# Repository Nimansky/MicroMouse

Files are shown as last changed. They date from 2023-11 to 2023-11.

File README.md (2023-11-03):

# MicroMouse - Readme

A [MicroMouse](https://en.wikipedia.org/wiki/Micromouse) built for a university school project by Nima Baradaran Hassanzadeh, Xian Chen and Christian Förster. The mouse is based on a Raspberry Pi 3B paired with an extension board hosting a STM32F030CC. As such, this project heavily involves sensor communication via I2C, inter-processor communication via UART, as well as a lot of STM32-internal timer and PWM logic. For exact specifics, please feel free to read the [documentation](/documentation.pdf)!

# Pinouts

| MCU Pin | Mode | GPIO Pin | Description |
|---|---|---|---|
| PF0 | Input | GPIO6 | Sensor links vorn |
| PC14 | Input | GPIO7 | Sensor rechts vorn |
| PC13 | Input | GPIO4 | Sensor links Seite |
| PB7 | Input | GPIO5 | Sensor rechts Seite |
| PB14 | TIM15 CH1 | GPIO0 | PWM Motor rechts (IN1) |
| PB15 | TIM15 CH2 | GPIO1 | PWM Motor rechts (IN2) |
| PB0 | TIM3 CH3 | LED1 | PWM Motor links (IN1)  |
| PB1 | TIM3 CH4 | LED2 | PWM Motor links (IN2)  |
| PA1 | EXTI Interrupt | GPIO13 | Motor Encoder rechts A |
| PC15 | EXTI Interrupt | GPIO14 | Motor Encoder links A  |
| PA0 | EXTI Interrupt | GPIO11 | Motor Encoder rechts B |
| PA2 | EXTI Interrupt | GPIO12 | Motor Encoder links B  |
| PB8 | I2C | SCL | Analog Sensor i2c SCL  |
| PB9 | I2C | SDA | Analog Sensor i2c SDA  |

# Communcation protocol

In order for the STM32 to be able to abstract away movement and the sensors from the actual solving algorithm, we had to come up with our own communication protocol.

## from master to mouse
    0x1A4 : Initiation sequence
    half byte : command type (current commands range from 0000-0100)
    32 bit param (padding if none needed)

## from mouse to master
    0x1A4 : Initiation sequence
    half byte : sensor (current sensors range from 0000-0110)
    32 bit sensor data

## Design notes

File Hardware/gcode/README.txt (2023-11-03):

Those parts were printed with a slightly modified Creality Ender 5 running Klipper.

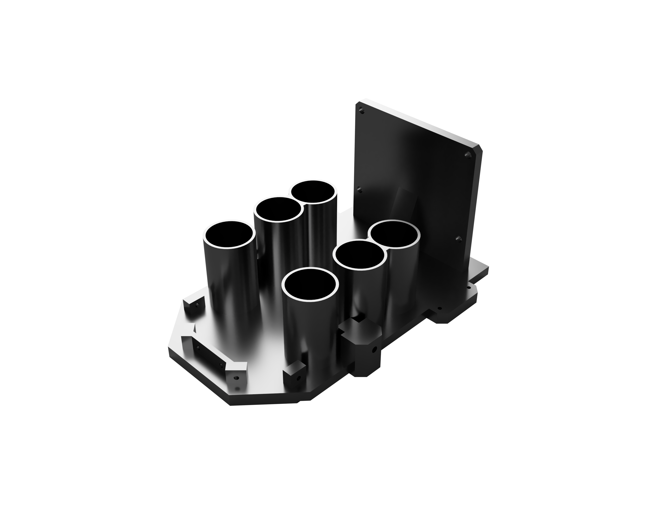
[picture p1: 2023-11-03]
Hardware/pictures/uMouse_base_plate.png

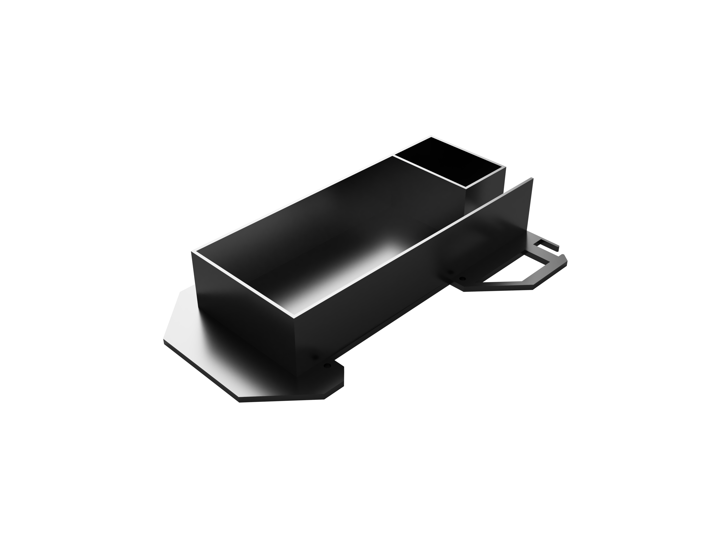
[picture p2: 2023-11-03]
Hardware/pictures/uMouse_top_plate.png

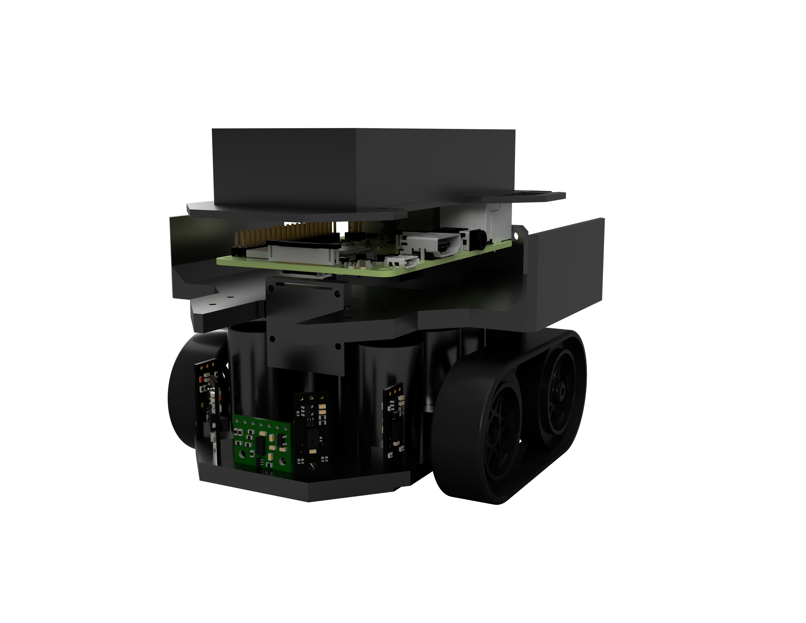
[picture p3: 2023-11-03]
Hardware/pictures/uMouse_total.png

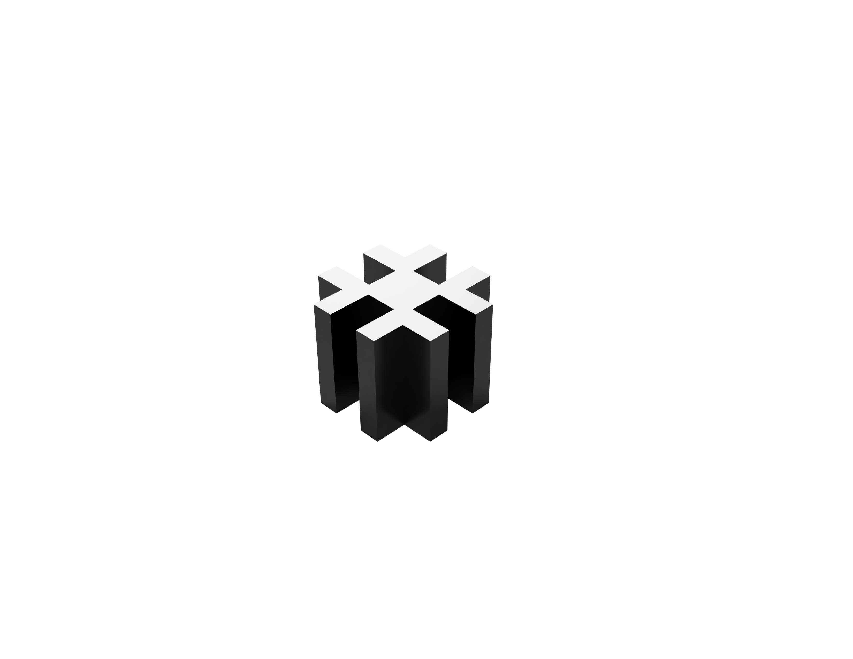
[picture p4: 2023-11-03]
Hardware/pictures/maze_connector.png

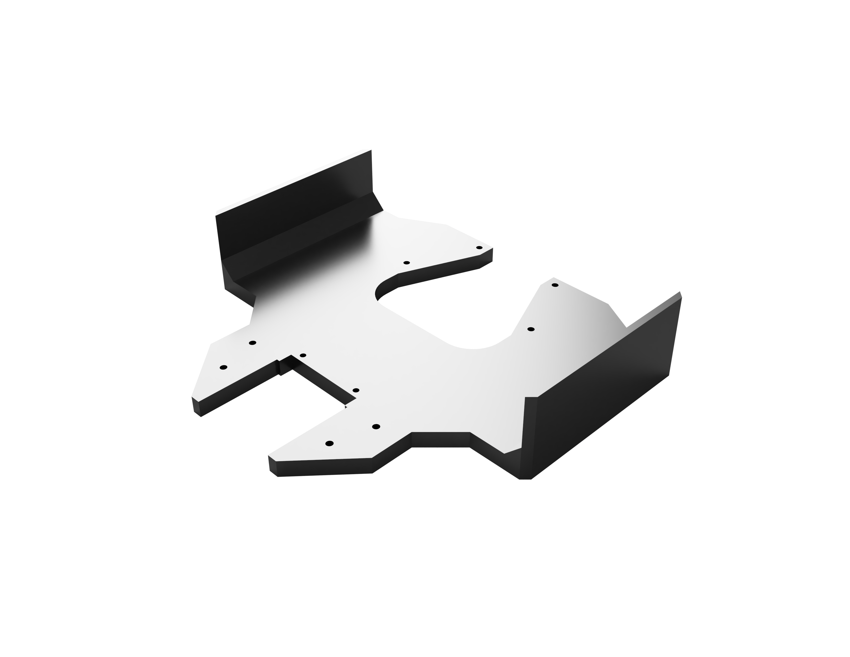
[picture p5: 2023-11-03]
Hardware/pictures/uMouse_mid_plate.png

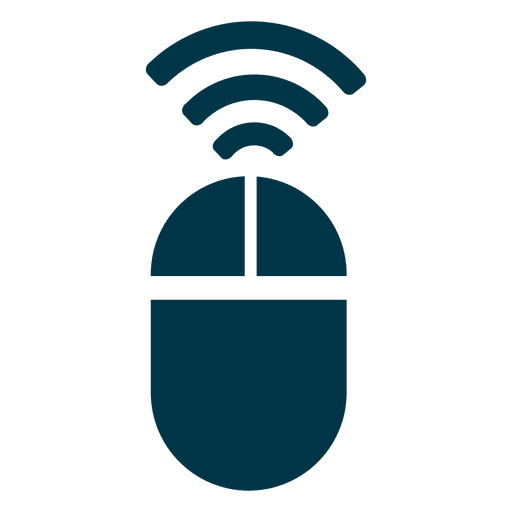
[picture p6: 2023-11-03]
Maze_Algorithm/res/mouse.png

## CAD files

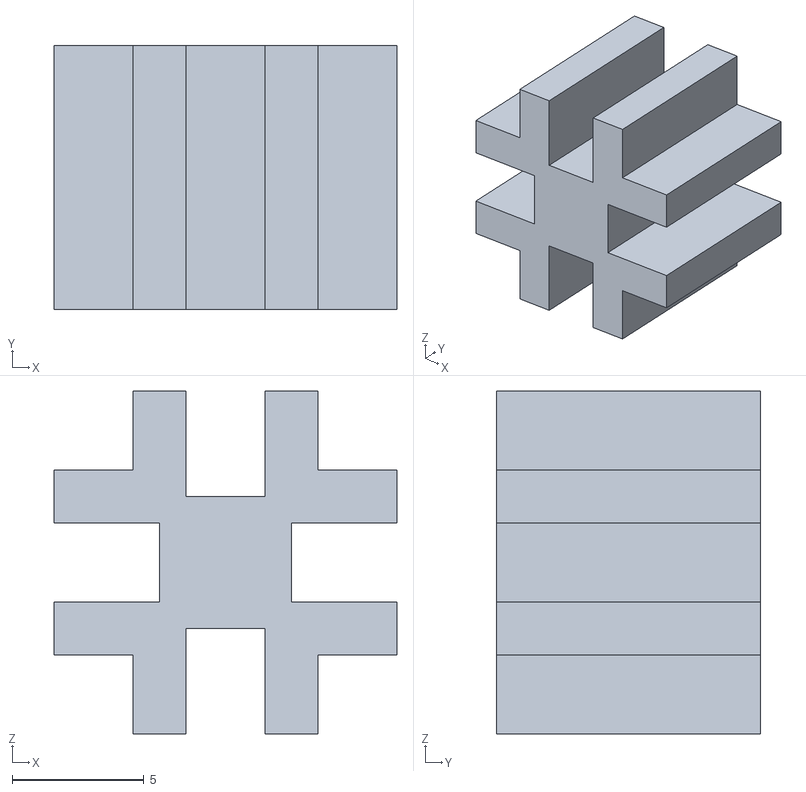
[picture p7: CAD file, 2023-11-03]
Hardware/models/maze_connector/maze_connector_v1.stl
13.0 x 10.0 x 13.0

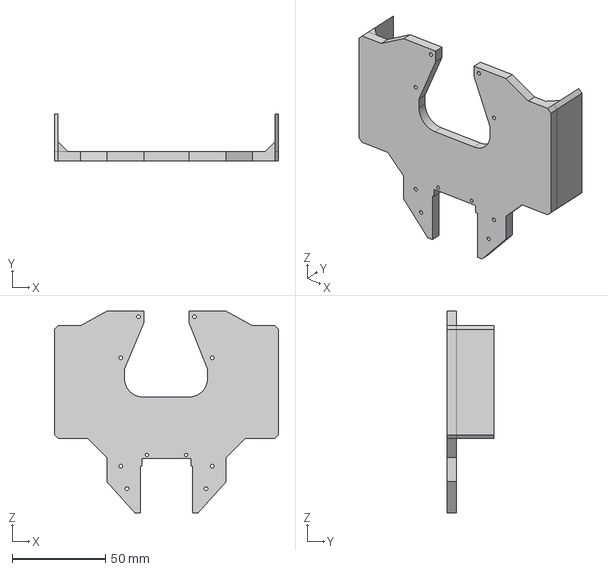
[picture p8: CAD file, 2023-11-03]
Hardware/models/mid_plate/mid_plate_v2.step
120.0 x 25.0 x 108.0 mm

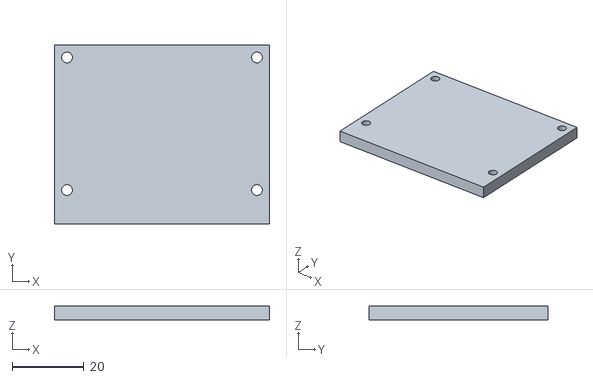
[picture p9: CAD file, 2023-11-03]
Hardware/models/misc/psu_mounting_test.stl
60.0 x 50.0 x 4.00

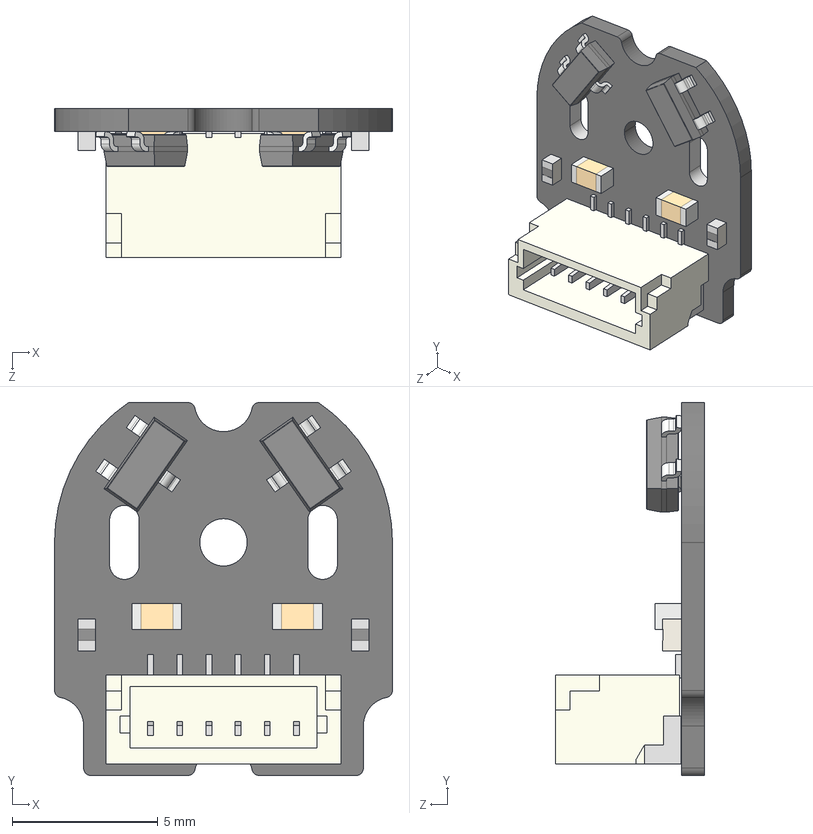
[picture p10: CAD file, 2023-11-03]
Hardware/models/pololu-4760-4761-models/magnetic-encoder-with-top-entry-connector-for-micro-metal-gearmotors.step
11.6 x 12.8 x 5.11 mm

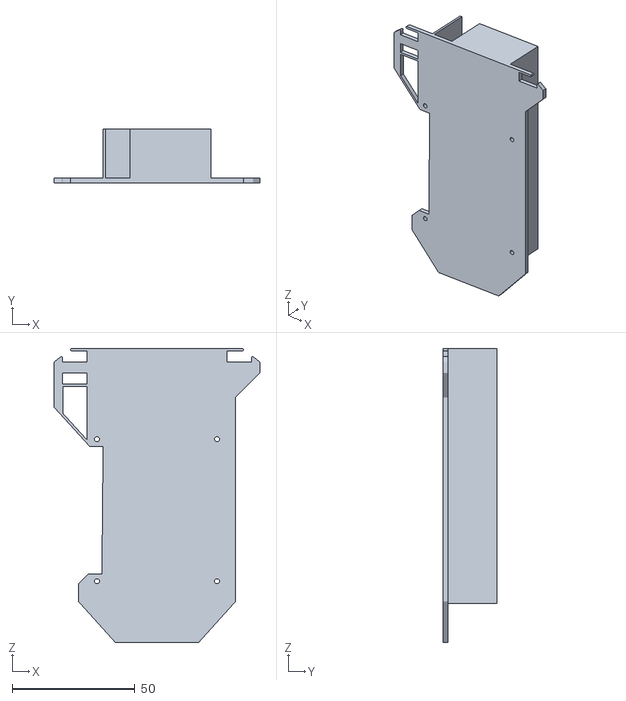
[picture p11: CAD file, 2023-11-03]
Hardware/models/top_plate/beta_top_plate_v2.stl
84.0 x 22.0 x 120.0

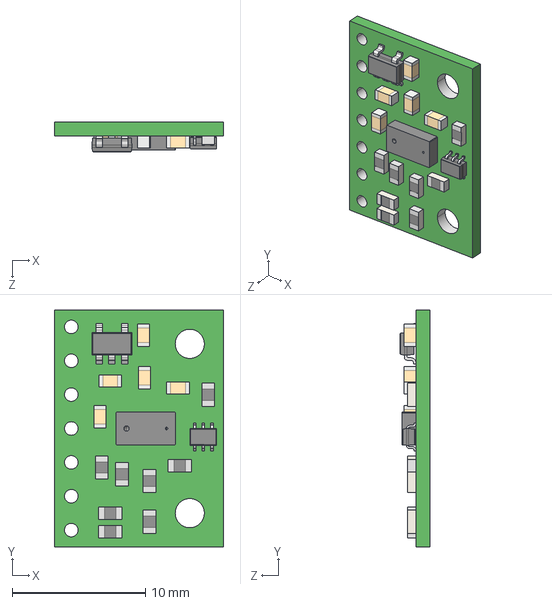
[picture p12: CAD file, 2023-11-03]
Hardware/models/vl53l0x-vl53l1x-vl53l3cx-carrier-model.step
12.7 x 17.8 x 2.21 mm

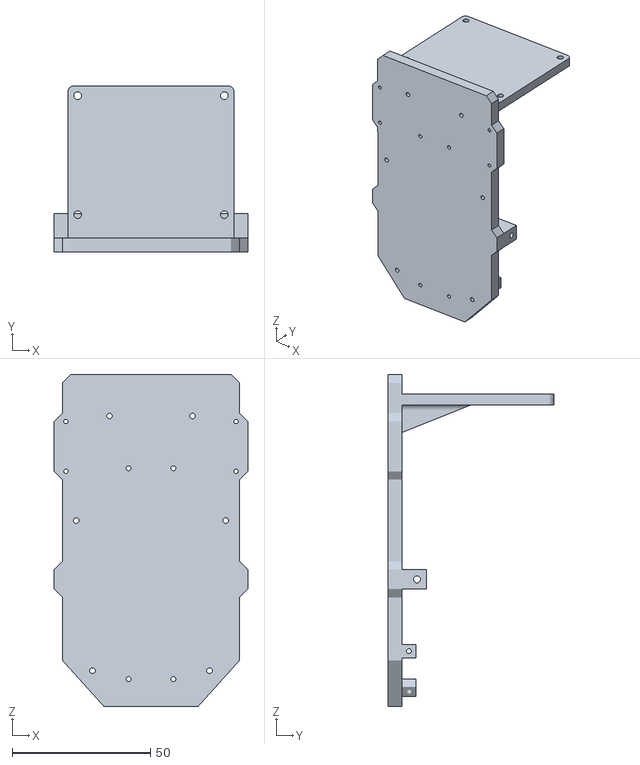
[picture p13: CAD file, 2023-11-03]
Hardware/models/base_plate/beta_base_plate.stl
70.0 x 60.0 x 120.0

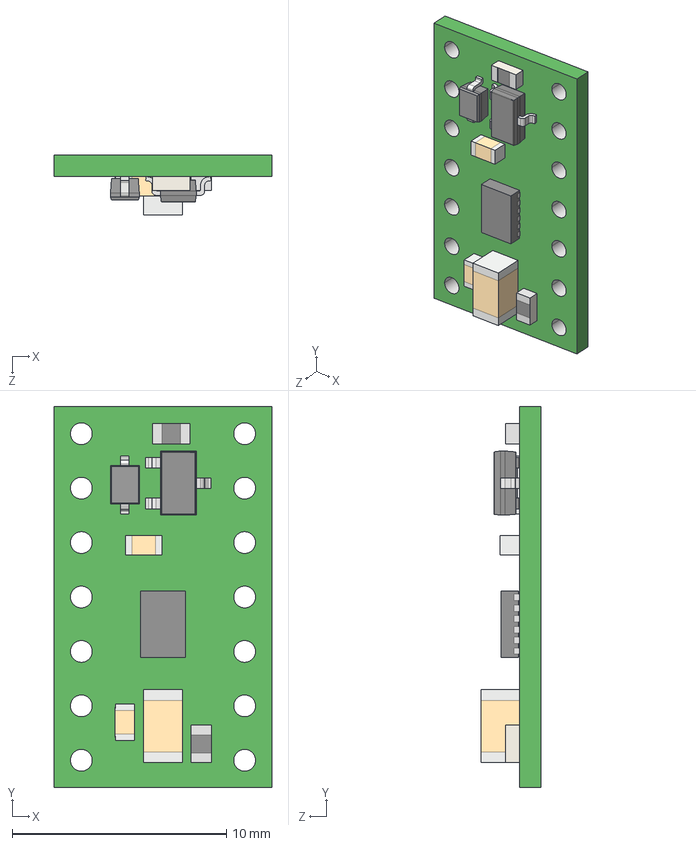
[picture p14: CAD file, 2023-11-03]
Hardware/models/drv8835-dual-motor-driver-carrier.step
10.2 x 17.8 x 2.82 mm

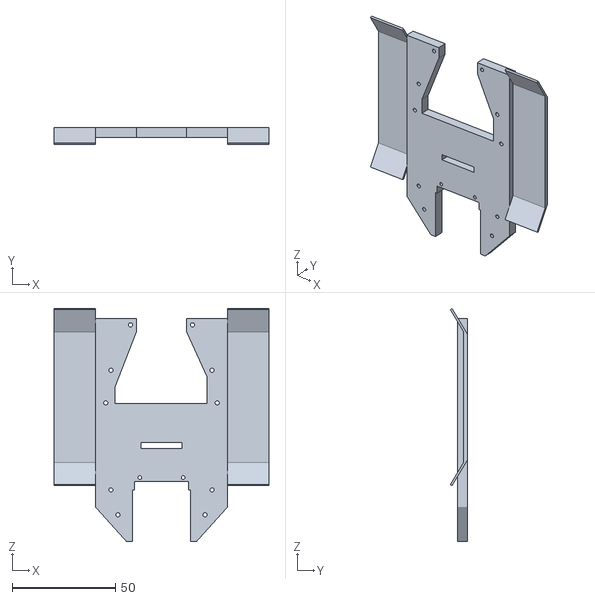
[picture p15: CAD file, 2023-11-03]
Hardware/models/mid_plate/beta_mid_plate.stl
104.0 x 8.46 x 112.9

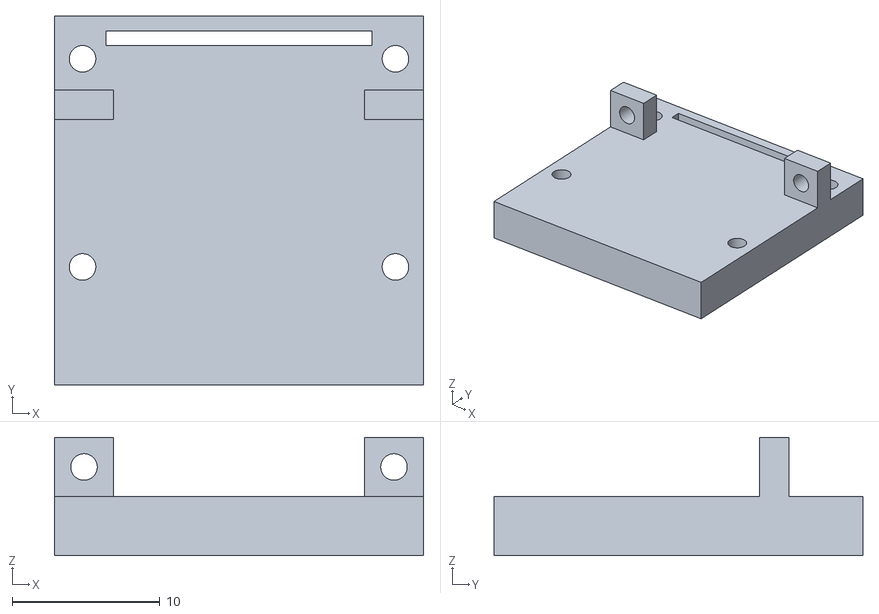
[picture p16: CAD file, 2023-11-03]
Hardware/models/misc/beta_cam_mount.stl
25.0 x 25.0 x 8.00

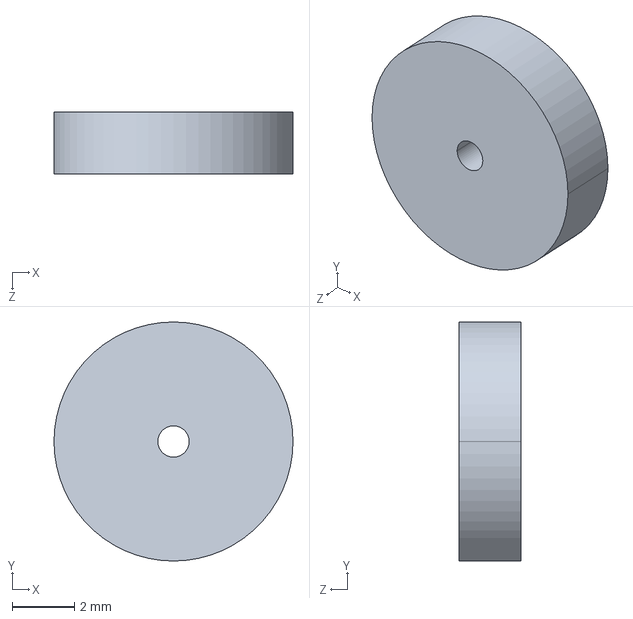
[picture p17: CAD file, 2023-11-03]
Hardware/models/pololu-4760-4761-models/magnetic-encoder-disc-for-micro-metal-gearmotors.step
7.65 x 7.65 x 2.00 mm

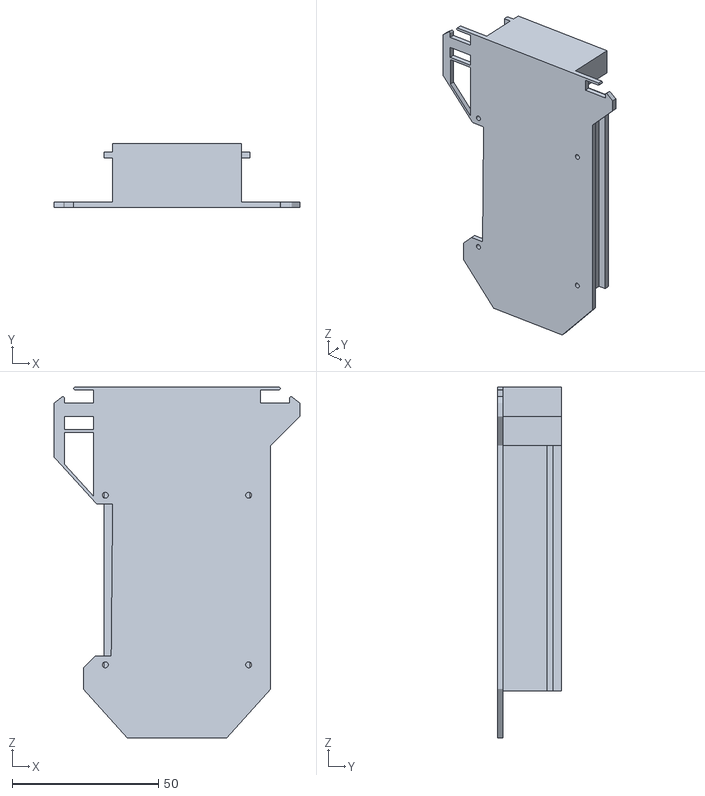
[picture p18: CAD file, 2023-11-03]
Hardware/models/top_plate/beta_top_plate.stl
84.0 x 22.0 x 120.0

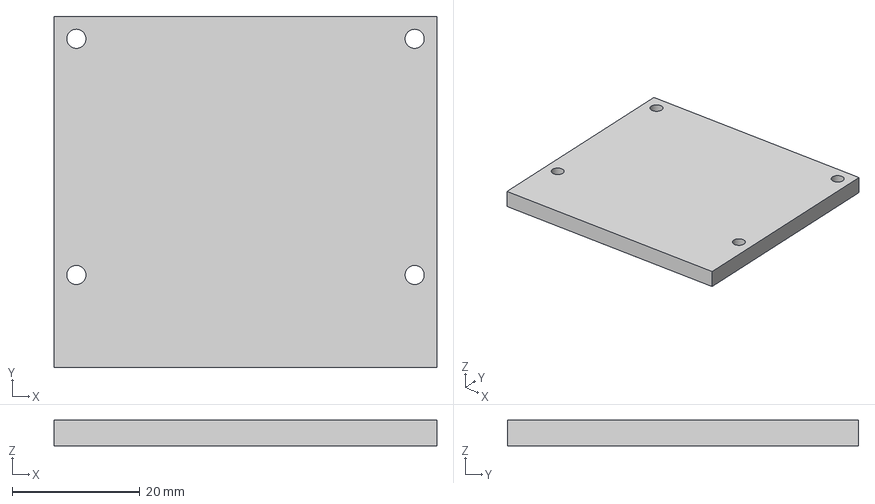
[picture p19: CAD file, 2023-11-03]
Hardware/models/misc/psu_bracket_test_base_plate_v7.step
60.0 x 55.0 x 4.00 mm

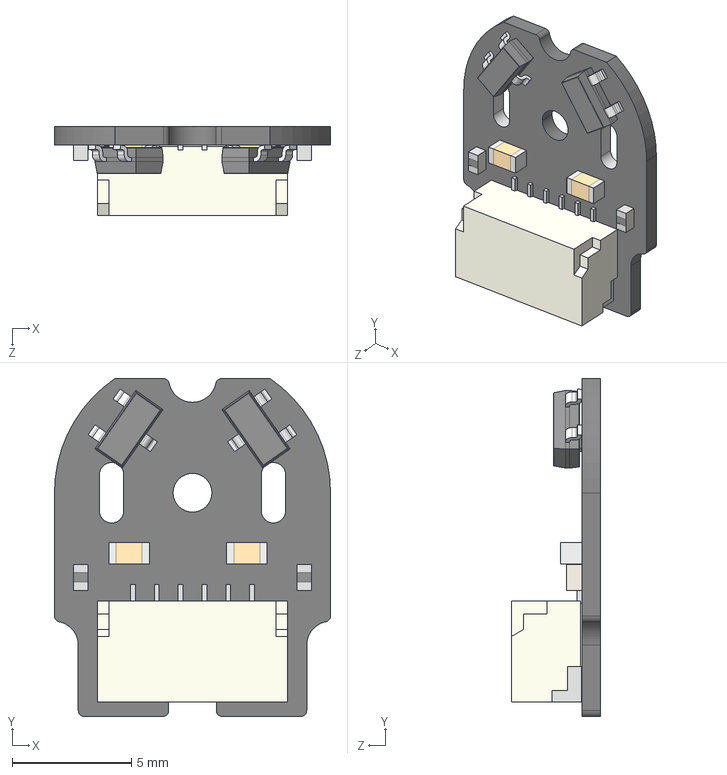
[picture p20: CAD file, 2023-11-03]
Hardware/models/pololu-4760-4761-models/magnetic-encoder-with-side-entry-connector-for-micro-metal-gearmotors.step
11.6 x 14.2 x 3.75 mm

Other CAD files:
Hardware/models/base_plate/beta_base_plate_v2.stl
Hardware/models/base_plate/base_plate_v7.step
Hardware/models/base_plate/base_plate_v5.step
Hardware/models/base_plate/base_plate_v4.step
Hardware/models/base_plate/base_plate_V3.step
Hardware/models/base_plate/base_plate_v6.step

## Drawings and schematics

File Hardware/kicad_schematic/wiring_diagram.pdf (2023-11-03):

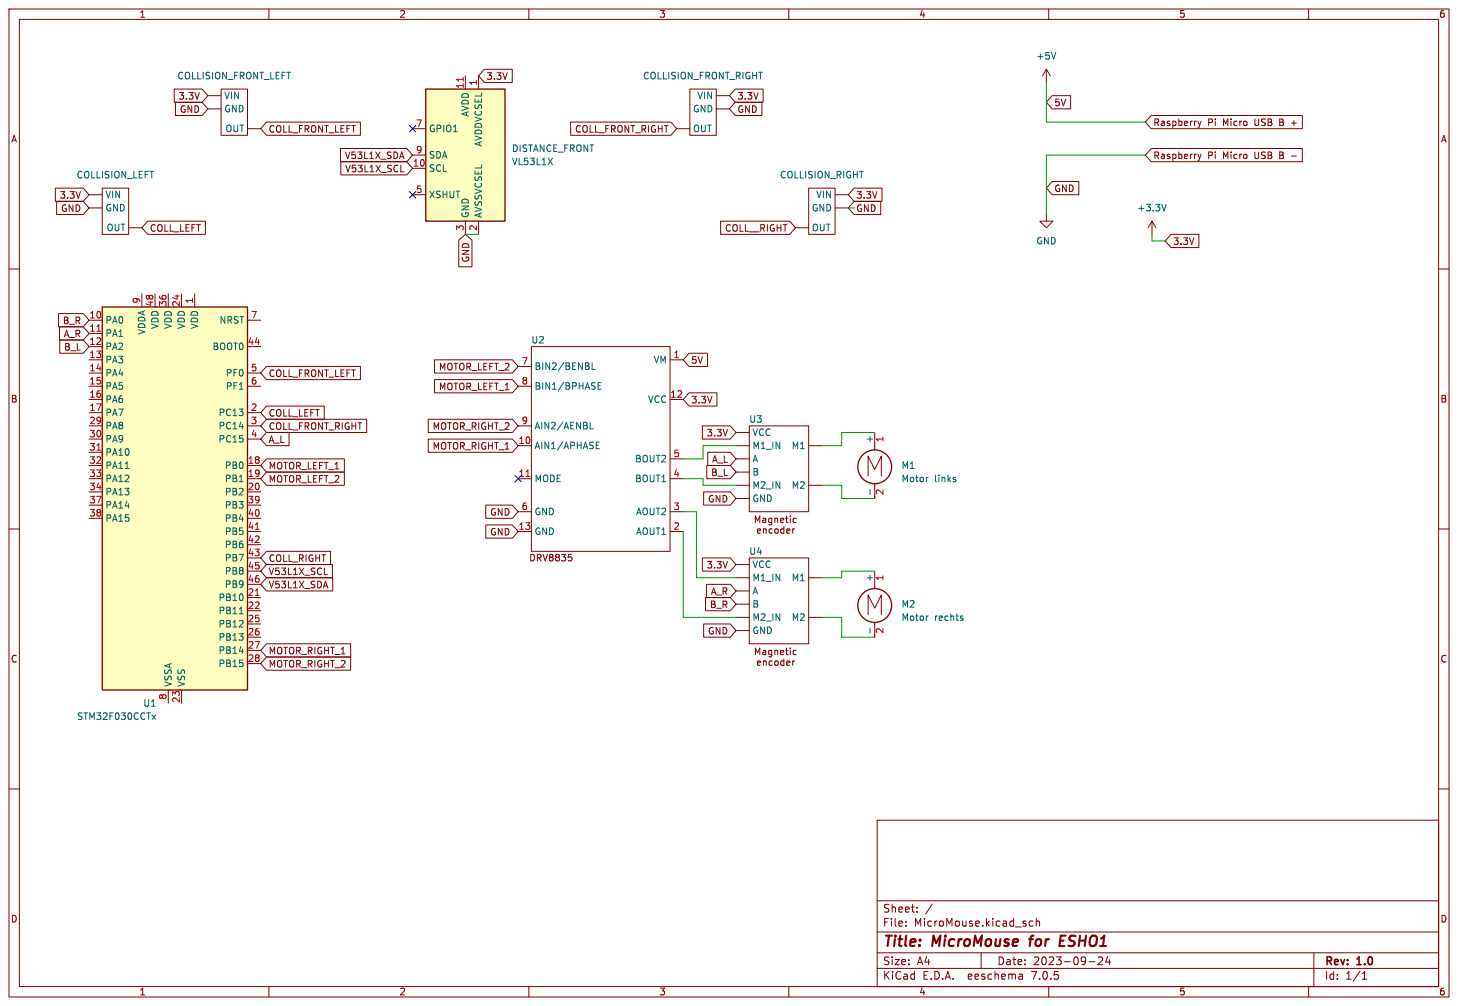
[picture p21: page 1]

9 U1 STM32F030CCTx DRV8835 VM 1 AIN1/APHASE 10 MODE 11 VCC 12 GND 13 AOUT1 2 AOUT2 3 BOUT1 4 BOUT2 5 GND 6 BIN2/BENBL 7 BIN1/BPHASE 8 AIN2/AENBL 9 U2 +5V GND OUT VIN

-2 M1 Motor links +3.3V GND OUT VIN

1 PA0 10 PA1 11 PA2 12 PA3 13 PA4 14 PA5 15 PA6 16 PA7 17 PB0 18 PB1 19 PC13 2 PB2 20 PB10 21 PB11 22 VSS 23 VDD 24 PB12 25 PB13 26 PB14 27 PB15 28 PA8 29 PC14 3 PA9 30 PA10 31 PA11 32 PA12 33 PA13 34 VDD 36 PA14 37 PA15 38 PB3 39 PC15 4 PB4 40 PB5 41 PB6 42 PB7 43 BOOT0 44 PB8 45 PB9 46 VDD 48 PF0 5 PF1 6 NRST 7 VSSA

File: MicroMouse.kicad_sch Sheet: / Magnetic

Id: 1/1 Title: MicroMouse for ESHO1

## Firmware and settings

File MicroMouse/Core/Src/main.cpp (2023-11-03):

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
/* Includes ------------------------------------------------------------------*/
#include "Motor.h"
#include "main.h"
#include "i2c.h"
#include "dma.h"
#include "tim.h"
#include "usart.h"
#include "gpio.h"
#include "Defines.h"
#include "CommandMessage.h"
#include "DataMessage.h"
#include "Executer.h"
#include "Motor.h"
#include "RotaryEncoder.h"
#include "AnalogSensor.h"
#include "vl53l1_api.h"


/* USER CODE BEGIN PV */

RotaryEncoder encLeft = RotaryEncoder(ENCLA_PIN, ENCLB_PIN, ENCLA_PORT, ENCLB_PORT);
RotaryEncoder encRight = RotaryEncoder(ENCRA_PIN, ENCRB_PIN, ENCRA_PORT, ENCRB_PORT);

// PIDController(encoder, kp, kd, ki)
PIDController pidLeft = PIDController(&encLeft, 0.2, 0.0, 0.0);
PIDController pidRight = PIDController(&encRight, 0.2, 0.0, 0.0);

Motor motorLeft = Motor(&htim3, TIM_CHANNEL_4, TIM_CHANNEL_3, &pidLeft);
Motor motorRight = Motor(&htim15, TIM_CHANNEL_2, TIM_CHANNEL_1, &pidRight);

AnalogSensor distanceSensor = AnalogSensor();

uint8_t Rx_buf[12]; //messages are 48 bit

bool stoppedMotorL = false;
bool stoppedMotorR = false;

/* USER CODE END PV */

void SystemClock_Config(void);
/**
  * @brief  The application entry point.
  * @retval int
  */
int main(void)
{
  /* MCU Configuration--------------------------------------------------------*/

  /* Reset of all peripherals, Initializes the Flash interface and the Systick. */
  HAL_Init();

  /* Configure the system clock */
  SystemClock_Config();

  /* Initialize all configured peripherals */
  MX_GPIO_Init();
  MX_TIM15_Init();
  MX_DMA_Init();
  MX_I2C1_Init();
  MX_USART5_UART_Init();
  MX_TIM1_Init();
  MX_TIM3_Init();
  MX_TIM6_Init();
  /* USER CODE BEGIN 2 */

  HAL_TIM_Base_Start_IT(&htim1);
  HAL_TIM_Base_Start_IT(&htim6);

  distanceSensor.init();

  HAL_UART_Receive_DMA(&huart5, Rx_buf, 6);

  /* USER CODE END 2 */

  /* Infinite loop */
  /* USER CODE BEGIN WHILE */
  while (1)
  {
    /* USER CODE END WHILE */

    /* USER CODE BEGIN 3 */
  }
  /* USER CODE END 3 */
}

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
/* USER CODE BEGIN 4 */

void HAL_GPIO_EXTI_Callback(uint16_t GPIO_Pin){

	//each rising and falling edge on the A  or B signal, update the encoder values
	if(GPIO_Pin == ENCRA_PIN || GPIO_Pin == ENCRB_PIN){
		encRight.update_encoder(GPIO_Pin);
	}
	else if(GPIO_Pin == ENCLA_PIN || GPIO_Pin == ENCLB_PIN){
		encLeft.update_encoder(GPIO_Pin);
	}

}

void HAL_TIM_PeriodElapsedCallback(TIM_HandleTypeDef* htim){
	if(htim == &htim1){
		//TIM1 interrupts at 10Hz (every 100 ms)
		encLeft.update_speed();
		encRight.update_speed();
		distanceSensor.update_sensor();


		collectSensorData();
	}

	if(htim == &htim6){
		//TIM6 interrupts at 1kHz (every 1 ms)
		if(motorLeft.isDriving()){

			motorLeft.recalcPIDSpeed();

			if(pidLeft.reachedSetPosition()){
				motorLeft.stop();
				stoppedMotorL = true;
			}

		}

		if(motorRight.isDriving()){

			motorRight.recalcPIDSpeed();

			if(pidRight.reachedSetPosition()){
				motorRight.stop();
				stoppedMotorR = true;
			}

		}

		if (stoppedMotorL && stoppedMotorR) {
			sendMessage(Message(MOVEMENT_DONE));
			stoppedMotorL = false;
			stoppedMotorR = false;
		}
	}

}

void HAL_UART_TxCpltCallback(UART_HandleTypeDef *huart){
	HAL_UART_Receive_DMA(huart, Rx_buf, 6);
}

void HAL_UART_RxCpltCallback(UART_HandleTypeDef *huart){
	if(huart == &huart5){
		//only if initiation sequence is correct
		if(Rx_buf[0] == 0x1A && (Rx_buf[1]>>4) == 0x4){
			uint8_t cmd = Rx_buf[1] & 0x0F; //cmd is just the lower 4 bits of the second byte
			uint32_t param = (Rx_buf[2] << 24) | (Rx_buf[3] << 16) | (Rx_buf[4] << 8) | (Rx_buf[5]);
			CommandMessage cmdMsg((Command)cmd, param);
			executeCommand(cmdMsg);
		}
	}
}

/* USER CODE END 4 */
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


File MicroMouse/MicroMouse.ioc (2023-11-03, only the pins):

Mcu.UserName=STM32F030CCTx
PA0.Signal=GPXTI0
PA1.Signal=GPXTI1
PA2.Signal=GPXTI2
PB0.Signal=S_TIM3_CH3
PB1.Signal=S_TIM3_CH4
PB14.Signal=S_TIM15_CH1
PB15.Signal=S_TIM15_CH2
PB3.Signal=USART5_TX
PB4.Signal=USART5_RX
PB7.Signal=GPIO_Input
PB8.Signal=I2C1_SCL
PB9.Signal=I2C1_SDA
PC13.Signal=GPIO_Input
PC14OSC32_IN.Signal=GPIO_Input
PC15OSC32_OUT.Signal=GPXTI15
PF0-OSC_IN.Signal=GPIO_Input

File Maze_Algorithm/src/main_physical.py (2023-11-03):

import sys
from time import sleep

from constants import *
from algorithm import Algorithm
from MicroMouseInterfacer import *
from adapter.micro_mouse_adapter import MicroMouseAdapter, FrontBlockedException

class PhysicalMouse(MicroMouseAdapter):
    def __init__(self) -> None:
        print("Physical Mouse initialized.")

    def get_sensor(self, *direction: list[Direction]):
        data = []
        for dir in direction:
            if dir == Direction.FRONT:
                print("reading FRONT")
                resp = read_sensor(Sensor.DISTANCE_FRONT)
                if resp[0]:
                    print(f"Success: {resp[1]}")
                    data.append(resp[1])
            elif dir ==  Direction.LEFT:
                print("reading LEFT")
                resp = read_sensor(Sensor.COLLISION_LEFT)
                if resp[0]:
                    data.append(resp[1])
                    print(f"Success: {resp[1]}")
            elif dir ==  Direction.RIGHT:
                print("reading RIGHT")
                resp = read_sensor(Sensor.COLLISION_RIGHT)
                if resp[0]:
                    data.append(resp[1])
                    print(f"Success: {resp[1]}")
            if resp != None and not resp[0]:
                raise Exception(f"Failed to read sensor of {direction}")
        return data

    def rotate(self, degree: float, speed: float):
        # Error correction for hardwaare
        offset = 240
        if degree > -1:
            turn_left(int((offset+degree)/90))
        else:
            turn_right(int(-(degree-offset)/90))

    def move(self, num_blocks : int = 1):
        # Error correction for hardwaare
        offset = 2
        resp = read_sensor(Sensor.DISTANCE_FRONT)
        # print(f"move() front distance: {resp[1]}")
        if resp[0] and resp[1] > PHY_DIST:
            move_forward(num_blocks*offset)
        else:
            raise FrontBlockedException()
    
    def move_backwards(self, num_blocks : int = 1):
        move_backwards(num_blocks)

if __name__ == "__main__":
    op_mode = input('What operation mode are we accessing? Maze solver (press 0) or a remote control (press 1)?\n')
    while not (op_mode == "0" or op_mode == "1"):
        op_mode = input("Please choose eihter 0 or 1\n")
    op_mode = int(op_mode)
    mouse = PhysicalMouse()
    if op_mode:
        while(True):
            key = input("Enter W to move forward, A and D to rotate and S to move backward.\nThen add an :[number] to signalize how much rotation/movement you desire!\n")
            if "escape" in key.lower():
                print("Exiting")
                break;
            key = key.split(":")
            mov = key[0].strip()
            nr = int(key[1].strip())
            if mov == 'w':
                print(f"Moving FRONT by {nr}")
                try:
                    mouse.move(nr)
                except:
                    print("Front is blocked! Can't move :(")
            elif mov == 'a':
                print(f"Rotating by {nr} degrees to the LEFT")
                mouse.rotate(nr)
            elif mov == 'd':
                print(f"Rotating by {nr} degrees to the RIGHT")
                mouse.rotate(-nr)
            elif mov == 's':
                print(f"Moving BACK by {nr}!")
                mouse.move_backwards(nr)
    else:
        new_maze = int(input("Are we exploring a new maze? 0 for 'no, old maze' or 1 for 'yes, we need to explore!'\n"))
        size = sys.argv
        if len(size) > 1:
            algorihtm = Algorithm(mouse, int(size[1]), new_maze=new_maze, avrg_dist=PHY_DIST)
            if len(size) > 3:
                algorihtm = Algorithm(mouse, int(size[1]), new_maze=new_maze, orientation=Orientation(int(size[2])), avrg_dist=PHY_DIST)
        else:
            algorihtm = Algorithm(mouse, 11, new_maze=new_maze, avrg_dist=PHY_DIST)
            
        while(not algorihtm.won):
            # sleep(2)
            input("Ready?")
            algorihtm.run()

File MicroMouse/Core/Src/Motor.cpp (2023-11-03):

/*
 * Motor.cpp
 *
 *  Created on: Sep 12, 2023
 *      Author: niman
 */

#include <Motor.h>

Motor::Motor(TIM_HandleTypeDef* PWMTimer, uint32_t forwardChannel, uint32_t reverseChannel, PIDController* pidController) {
	tim = PWMTimer;
	fwdChan = forwardChannel;
	revChan = reverseChannel;
	pid = pidController;
}

void Motor::recalcPIDSpeed(){

	float pidSpeed = pid->calculateSignal();
	int sign = (pidSpeed > 0) - (pidSpeed < 0); //1 for pos, -1 for neg, 0 for 0
	pidSpeed = fabs(pidSpeed) > 1.0 ? 1.0 : fabs(pidSpeed);

	setSpeed(pidSpeed * sign * dir);
	pid->setEncoderDirection(sign);
}

/*
 * numFields: number of maze fields to proceed
 * direction: 1 for forwards, -1 for backwards
 */
void Motor::drive(uint32_t counts, int8_t direction){

	if(driving) return;

	pid->setSetPosition(counts); //setposition is amount of counts to turn the wheel to
	pid->resetEncoderDistance(); //reset traveled distance to 0

	dir = direction;

	recalcPIDSpeed();

	start();
}

bool Motor::isDriving(){
	return driving;
}

/**
 * sets the speed of the motor to anything between -1 and 1 * maxSpeed
 * note: 0 is not a valid argument to pass, since to stop the motor, the method Motor::stop() should be called
 */
void Motor::setSpeed(float speed){
	float absSpeed = fabs(speed);
	if(speed >= -1.0 && speed < 0){ //case reverse
		switch(revChan){
		case TIM_CHANNEL_1:
			tim->Instance->CCR1 = (65535 * absSpeed)-1;
			break;
		case TIM_CHANNEL_2:
			tim->Instance->CCR2 = (65535 * absSpeed)-1;
			break;
		case TIM_CHANNEL_3:
			tim->Instance->CCR3 = (65535 * absSpeed)-1;
			break;
		case TIM_CHANNEL_4:
			tim->Instance->CCR4 = (65535 * absSpeed)-1;
			break;
		}
		switch(fwdChan){
		case TIM_CHANNEL_1:
			tim->Instance->CCR1 = 65535;
			break;
		case TIM_CHANNEL_2:
			tim->Instance->CCR2 = 65535;
			break;
		case TIM_CHANNEL_3:
			tim->Instance->CCR3 = 65535;
			break;
		case TIM_CHANNEL_4:
			tim->Instance->CCR4 = 65535;
			break;
		}
	}

	if(speed > 0 && speed <= 1.0){ //case forward
		switch(revChan){
		case TIM_CHANNEL_1:
			tim->Instance->CCR1 = 65535;
			break;
		case TIM_CHANNEL_2:
			tim->Instance->CCR2 = 65535;
			break;
		case TIM_CHANNEL_3:
			tim->Instance->CCR3 = 65535;
			break;
		case TIM_CHANNEL_4:
			tim->Instance->CCR4 = 65535;
			break;
		}
		switch(fwdChan){
		case TIM_CHANNEL_1:
			tim->Instance->CCR1 = (65535 * absSpeed)-1;
			break;
		case TIM_CHANNEL_2:
			tim->Instance->CCR2 = (65535 * absSpeed)-1;
			break;
		case TIM_CHANNEL_3:
			tim->Instance->CCR3 = (65535 * absSpeed)-1;
			break;
		case TIM_CHANNEL_4:
			tim->Instance->CCR4 = (65535 * absSpeed)-1;
			break;
		}
	}
}


void Motor::start(){
	driving = true;
	HAL_TIM_PWM_Start(tim, fwdChan);
	HAL_TIM_PWM_Start(tim, revChan);
}


void Motor::stop(){
	driving = false;
	HAL_TIM_PWM_Stop(tim, fwdChan);
	HAL_TIM_PWM_Stop(tim, revChan);
}


Motor::~Motor() {
	// TODO Auto-generated destructor stub
}

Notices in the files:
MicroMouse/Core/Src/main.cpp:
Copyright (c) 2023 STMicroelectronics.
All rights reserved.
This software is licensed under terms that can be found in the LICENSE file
